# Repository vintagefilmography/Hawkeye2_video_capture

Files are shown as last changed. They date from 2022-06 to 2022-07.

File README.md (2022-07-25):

# SMC02 video capture
This setup consists of a modified projector and the T3i Canon camera. The setup provides the 8mm film capture running at 3FPS and outputs the video in ML (Magic Lantern) RAW format in 1728x972 resolution.  
The purpose of this  readme is to provide the instructions to the user on how to modify the existing 8mm film projector for the video capture directly into the camera using a small off the shelf stepper controller.  
Similar to other projects of this type, this one also requires several modifications to the projector including the light change, and motor change but unlike other projects of this type it provides the DSLR camera capability and RAW video format. The DSLR is used in a slow video mode. 
The stepper controller is programmed to precisely control the stepper motor rotation to provide the proper FPS which matches the FPS of the camera with no flicker. 
System Components  

system-assembly

## Stepper Controller  
At the heart of the system is the SMC02 stepper controller. 
https://www.ebay.com/itm/175028855543

## Stepper Motor  
Use the following stepper.
2.7A for this type motor https://www.amazon.com/gp/product/B00PNEPF5I/
Other steppers may also work but are not covered in this readme.  
If you are planning to pull the projector transport out, then you can use the mounting bracket from this repo.  Check the mechanical parts folder. 

## Pulley
This pulley is recommended. You will also need a sleeve because the pulley bore is slightly larger than the motor shaft. 
Check t mechanical folder for the sleeve sdl.
https://www.amazon.com/gp/product/B07C4QD1BV/

## Belt
This used to be a big problem but with the neophrene Urethane belting that became available it is easy to make your own custom belt.
https://www.amazon.com/gp/product/B07L3W7Z1N  
Follow the following instructions:  
https://www.youtube.com/watch?v=mBtHvPWVgDw

## Assembly
Print out all of the parts from the mechanical folder. If you do not have the printer then you can get them done outside but it will become rather costly. Getting a new 3D printer will probably be cheaper in a long run.
Use a 14"x10"x0.63": piece of wood to mount the components on.  
https://www.homedepot.com/p/Rubbermaid-Black-Laminated-Wood-Shelf-10-in-D-x-36-in-L-4B2500BLA/100200907
Additionally cut two additional pieces of wood size 7"x7"x0.63"and 7"x3.6"x0.63". These will be used as a standoff for the projector transport. 
This will work for the Chinon 2500GL but if other type of projector is used then you will have to figure out how high the the transport has to sit for the proper alignment with the camera.
Assemble the three pieces of wood as shown.
base
Mount the projector transport bracket to the base as shown.
transport_bracket_assembly
Mount the transport onto the bracket using the original transport mounting screws.
The transport mounting will need additional support to prevent the film shake. Use an L bracket  
https://www.homedepot.com/p/Everbilt-3-in-Black-Corner-Brace-4-Pack-13741/300985591
and mount it as shown. Install the spacer underneath the bracket so that the transport sits perfectly vertical. The spacer is included in the mechanical folder. If the transport is not vertical then adjust the spacer accordingly. Tilted transport will cause focus issues.
L-bracket1

Mount the macro lens onto the camera.  
Mount the camera onto the slider.  
Turn the camera on and position it so that the film gate is visible and adjust the zoom so that the film gate covers most of the camera display. Set the slider knobs about half way of the travel. Now, slide the camera on the base board left and right and forward and backwards until the gate is centered in the camera display. Mark the position of the slider  on the base board.  
Remove the camera from the slider.
Place the slider upside down on the table and place a piece of white paper over it. Trace the outline and teh mounting holes as the first graders do.  
https://craft-art.com/tracing-pictures/  
Cut the outline with the scissors and place it on the board so that it is aligned with the marked up outline on the board done in the previous step. Drill the holes. Remove the paper template and mount the slider onto the board using the appropriate size screws.  
Light Mounting.    
The light has to be mounted in front of the gate.    
(This is still work in progress -- will be updated shortly)    
Takeup reel mount.    
Use the microphone stand  
https://www.amazon.com/dp/B07F82BPLV  
Remove the microphone adapter and install the takeup motor bracket.   
Mount the takeup motor onto the bracket using the M3x8 screws  
https://www.amazon.com/gp/product/B076J3W7R4  
Slide the takeup spindle over the motor shaft.  
Slide the takeup reel over the spindle.  
Install an M3 wingnut onto the M3x25 flathead screw and tighten it.  
Slide a flat M3 washer over the screw shaft to create the "clutch" mechanism.  
Push the screw through the spindle center until it engages with the motor shaft.  
Turn the wingnut in until snug. The tightness will determine the amount of pull on the film.  
You do not want it too tight becaue it can cause film damage.  
Solder two wires to the motor terminals.  
Connect the wires to the speed controller.  
https://www.amazon.com/gp/product/B071H2YQG5/  
Connect the controller to the 12VDC source.  

Proceed similarly with the supply reel. 
Remove the mic adapter from the microphone stand. install the reel mount assembly onto the mic stand.
Install the small clip onto the reel spindle using a small metal pin. 
https://www.amazon.com/Neiko-50412A-Assortment-Storage-Pieces/dp/B076B4WT1V/

supply-reel-mount_assy
Controller installation  
Afix the mounting bracket onto the base board by using two wood screws.
Mount the SMC02 cntroller onto the controller mount but sliding it into the mount opening all the way until locked in. 
Wire up the controller as shown.
smc02-wiring

Stepper Installation  
Mount the stepper onto the stepper racket using the M4 screws and nuts.
Mount the sleeve over the motor shaft and then side the pulley over the sleeve. Do not tighten the locking slugs. 
Align the pulley with the transport cam and install the belt. Slide the stepper assembly left and right on the base board until the belt is aligned and has 
good enough tension on it. Mark up the stepper bracket location.  
Remove the stepper from the bracket and install the bracket by using 2 wood screws. Mount the stepper back onto the bracket and install the belt.

## Tuning the Stepper  
The FPS (fremes per second) of the film transport is not the same as the stepper RPS (revolutions per second) due to different pulley diameters.  
The ratio has to be determined experimantally.  
Connect the controller to a 24VDC source and turn the power on.  
The display should show initial operaional settings.  
initial-display  
Press and hold the control knob until the unit goes into the setup mode.  
setup1  
turn the knob clockwise until F03 is displayed.  
The bottom line will show the default 010.0  
Pres the control knob again to enter the bottom line edit mode.  
The decimal value will be flashing.  
The decimal value can be changed by rotating the control knob, but leave it at zero.  
Press the knob again and the least significant digit will be flashing. Change it to 9.  
Press again and change the next digit to 2.  
Press again and change the first digit to 3.  
The lower display should  be reading 329.0 with number 3 flashing.  
Do the extended press to get out of the setup mode.  
Now 329.0 should be displayed on the top line and 0000 on the bottom line.  
That sets the stepper RMP.  
Now we have to set the running mode for continuous operation.  
Do the extended press again to get into the setup mode.  
F01 will be displayed on the top line and P01 on the bottom line.  
Press the control knob and the bottom line should be flashing.  
Change the bottom to P03 by rotating the control knob.  
Do the extended press to get out of setup.  

Quick Test  
Press the CW button - the motor should run clockwise and the film cam should rotate at 3 RPM.
Press the stop button. The motor should stop.  
Note: If the motor rotation is reversed then reverse the green and black wire connections.
Another Note: The reverse speed is set to 10 rpm which is slow. If planning to use the reverse operation then the reverse speed is set by changing the F05 field  
by using similar procedure as listed above.  

## Camera  
The camera used should be capable of caustom frame rates. 
Sony A7iii supports custom rates but it is quite expensive.
An alternative is to obtain the T3i body and add the macro lens. 
The stock camera does not support the custom frame rates but there is a custom software available that enables   
custom frame rates and raw video.
Listed below are the instrustions on how to install Magic Lantern and set it up for FPS override, but before that here is a quick overview:  
Download the build to your PC and unzip it.
Format the SD card by the camera itself.
Make sure your battery is fully charged. That is very important. You can ruin the camera if you do not follow these instructions carefully. 
Install the SD card into the camera and power it up.  
BTW - going forward any time you open the SD card cover, do not remove the  SD card immediately, wait for the red led to stop flashing.
Set the camera to Manual mode
Press the MENU button 
Go to the second last screen and press the Firmware button.
Double check the Magic Lantern instructions  
https://builds.magiclantern.fm/600D-102.html  
Do the update  
Recycle power and you are ready to go.  

Refer to https://magiclantern.fm/  
for more details.  
Specifically refer to this page for the T3i:  
https://builds.magiclantern.fm/600D-102.html  
For setting up the camera refer to:  
https://www.youtube.com/watch?v=NYGseJ7Sofk  
https://www.youtube.com/watch?v=RvZHmOgzm2Q&t=6s  
Thsese two videos give you a pretty good idea on how to set the 3 FPS but there are some devil details missing.  
Will try to cover those in here.  
Set the camera to Movie mode.  
Turn the camera on and turn on live preview.  
This will start the Magic Lantern software.  
Then press the delete button.  
The settings screen will pop up.  
Go to  the Movie screen:  
movie-setup  
Select FPS OVerride. Press enter to turn it on.  
fps-override-on  

Then press the Q button on the T3i. Other camera types will have a similar button.  
The FPS Override screen will pop up.  
fps-override-2point5  
Hit the Q button.  
fps-set  

Position highlight over desire FPS and hit Enter. Set desired FPS to 3 by using the left and right keys.
  
 fps-set-to-3  
Press enter again to go bach to the FPS Override screen. Select the "Optimize for" entry and hit Enter.

optimize  

Select High FPS  

high-fps  

After selecting High FPS the camera will go back to the FPS override screen.  

fps-override-1  

Select Advanced Mode.  

advanced-mode  

Select Timer B. Leave it as is for now but remebmer how you got to this point becase you will need it later   
for sync procedure.

tune-fps  

Go back to the FPS Override screen.  

fps-override-2  

The shutter speed can be changed on the Expo screen.  

shutter  

The shutter rspeed can also be changed while scanning the film by using the main dial. Check the manual fo main dial location (tp of the cam).
The light should be bright enough so that the shutter speed is 1/300 or faster. If the shutter is too slow than some image degradation can happen.
It is to be noted that even at this fast shutter setting, due to low FPS you could experience some jello effect. The jello effect exhibits itself as a 
the video shrinking and expanding as jello and can be very annoying. The cause is the rolling shutter which stores one image line at a time. At slow scan   
there is a shift in the top of the image as compared to the bottom of the image i.e. by the time the scan gets to the bottom the scene has changed somewhat.   
But on a positive note, the postprocessing done in DaVinci Resolve almost completely eliminates this degradation.   

## Macro Lens
There are many out there that will do the job.  
Venus Laowa is a pretty good pick. It has more than enough magnification and good image quality and it is reasonably priced.
https://www.venuslens.net/product/laowa-25mm-f-2-8-2-5-5x-ultra-macro-2/  

## Sync procedure
Back it off and turn it away from the gate and point it to the cam (pulley). Adjust the speed control on the controller until the cam appears stationary. Actually it will jump up and down and possibly drift slowly. If the drift cannot be stopped by the speed control, then adjust the Magic Lantern Timer B to minimize the drift. Once done, refocus the camera back onto the gate. With this procedure I can run for several thousand frames without sync issues. It should be noted that the transport should be in good condition ensuring constant speed. It still may be possible that the drift catches up with you depending on the initial condition. In that case just run one step up for a few minutes if the drift is from the top, or one step down if the drift if coming from the bottom. Then switch back to the original speed. After that you can run for several thousand frames without sync issues


## Operation

Load the film.  
Plug in the 24V and 12V external power sources. 12V is for the takeup and 24 is for the controller.     
Make sure that they are not reversed which can result in the takeup motor damage. 
Turn the light on.  
Connect the camera HDMI port to a monitor.  
Turn the camera on and press the live view button. This will start Magic Lantern. 
Press Live View again to start recording.  
Press  the CW button on the controller.
Once done with the recording, stop the camera by pressing the live view again abd stop the controller by pressing the stop button.  
Remove the SD card and copy the MLV (Magic Lantern Video) to a PC.  

## Post Processing  
Download the MLV app from:  
https://mlv.app/  
Install the app.  
Open it up.  
Drag the video into the session window as shown:  
mlv-drop-video  
Expand the transformation entry on the right hand side and turn the Upside down control on.  

upside-down  
Review the video to see if any sections have to be retaken. This app has pretty limited video edit capabilities  
but it has lots of export formats suitable for popular video editors.  
Open up export settings from File pulldown:  
  
Select DNG uncompressed format if exporting to Resolve.  
The DBG images take up lots of space but in return contain the raw information that can be utilied in DaVinci Resolve.  

Export the video by using File->SaveVideo into the directory of your choice.  
Close the mlvApp.  

## DaVinci Resolve  
Open up Davinci Resolve and drag the DNG images into it.
  
  
Right click on the clip and create the new timeline:  
  
Click on Custom Settings and change the frame rate to what you need.
Switch to Edit Mode:  
  
In the transform area on the right hand side, rotate the video by 180 degrees.  
  
Switch to color edit mode. Select Camera Raw and Decode using Clip as shown:  
  
Adjust exposure as shown:  
  
If the video shows a jello effect then this would have need adjustment.  
Go back to the edit mode:  
In the transform area on the right hand side scroll down to Stabilization.  
Set mode to Perspective.  
Turn on zoom and then adjust stabilization parameters as needed. It will be a trial and error process. Too little and the  
video will be wavey and too much will cause severe clipping and loss of resolution.  
  
Click on the stabilize button to run stabilization. It may take a while. 

https://www.youtube.com/watch?v=u6UWJCQB7n0  
If the video has noticable jello effect then apply the Resolve stabilizer as shown the video below.  
https://www.youtube.com/watch?v=73zwjGcbhP4  

### Slow Motion interpolation with speed change  
Save the VirtualDub2 video as a sequence of tiff images first.  
Select all images and drag them into the media window of DR (DaVinci Resolve).  

You will get the images shown as a clip in the media window.  
  
 
Right click on the clip, select the click attributes and set the frame rate if necessary  
but you can leave it as is since the frame rate change can be done later.  
Right click on the clip and create the timeline from it.  
  
   
Switch to Edit Mode.  
  
   
Click on project settings  
  

Scroll the settings all the way down and change the retime process to optical flow (more info available here  
htps://www.youtube.com/watch?v=m5cO3ZTfSr4 ).  
  
  
Save the settings.  
Now, right click on the clip and change the speed to whatever FPS needed.  
  
 
Change the FPS to whatever required.   
  
 
Make sure that Ripple sequence is checked off. If not the clip duration will not change and the clip will be truncated.   
Click on the change button. Note the clip duration change in the timeline window.  
  
   
Once done, complete other changes as necessary and then export the video by switching to deliver mode.  
  
   
Change the video format to whatever you like.  
  

Add to render queue  
  
 
And then start render.  
  

### Interpolation without Speed Change  
The above instructions were for interpolated frames that result in smooth slow motion speed.  
In many cases however we want to interpolate the frames but want to maintain the original speed.  
In order to do that just follow the above instructions but do the following changes.  
1.	Make sure your project settings are set to optical flow for retiming.  
2.	Before creating the timeline set the clip attributes FPS to 60 FPS.  
3.	Create new timeline  
4.	Using the above procedure change timeline speed to 24 FPS or whatever final speed you need  
The rest is the same as the above procedure.   
Here are the details.  
Project settings optical flow selection.  
    
    

Drag the images into the media window. Make sure all images are selected.  
  
   
Switch to edit mode if not already there.    
  
   
 Right click on the images file in the media window and select clip attributes.  
 Set clip FPS to 60 or whatever interpolation rate you prefer.  
   
Click on OK.   
Right click on the clip again and create the timeline. The timeline create window pops up.  
Click on custom settings.  
  
 
It is to be noted that in version 17.2 of DaVinci the timeline popup window is a bit different.  
It does not have custom settings but it has a button to use the Poject Settings.  
Make sure that button is not checked off. 
  

Select Format tab and set the desired interpolation FPS.  
  
 
The new timeline will show up in the timeline window.  
Right click on the timeline in the timeline window and select Change clip speed.  
  

Change clip speed back to normal speed i.e. 24 or 18 FPS or whatever the original speed was.   
You can also go lower if slow motion is preferred. Make sure Ripple sequence is checked off.  
  
 
Note the clip stretching out after the speed change.   
If t does not then make sure that Ripple sequence is checked off.  
At that is basically it.   
You can test run the clip to make sure that additional frames got added by stepping through the video (left, right arrows).  
The next step is to render and save the video.  
Switch to Deliver Mode.  
  
   
Select proper video format and add to render queue. 
  
   
Start rendering.  
  
 
And that completes the procedure.

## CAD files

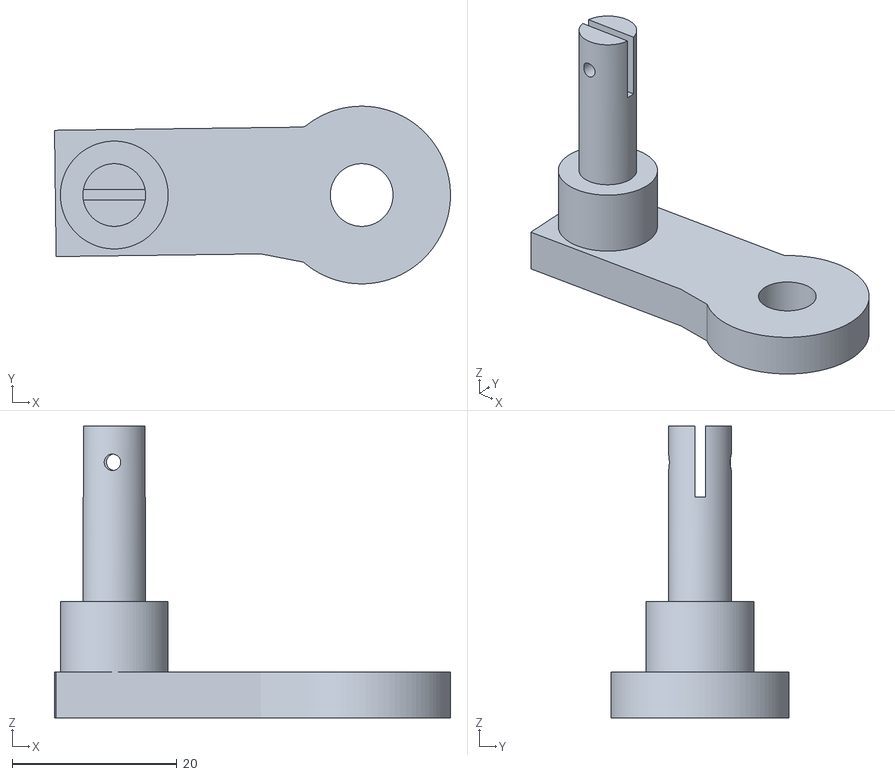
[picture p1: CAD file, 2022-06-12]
mechanical/reel-mount_assy.stl
48.1 x 21.6 x 35.4

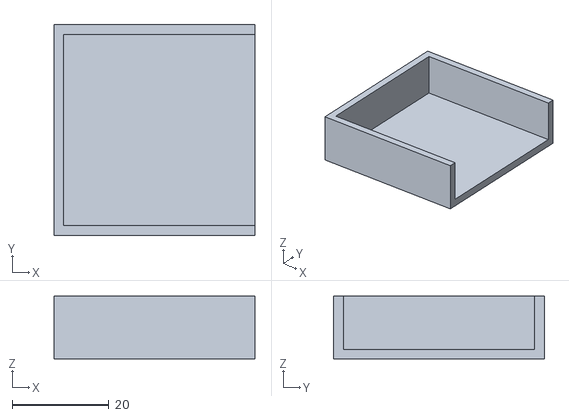
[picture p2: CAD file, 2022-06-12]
mechanical/diffuser.stl
41.5 x 43.5 x 13.0

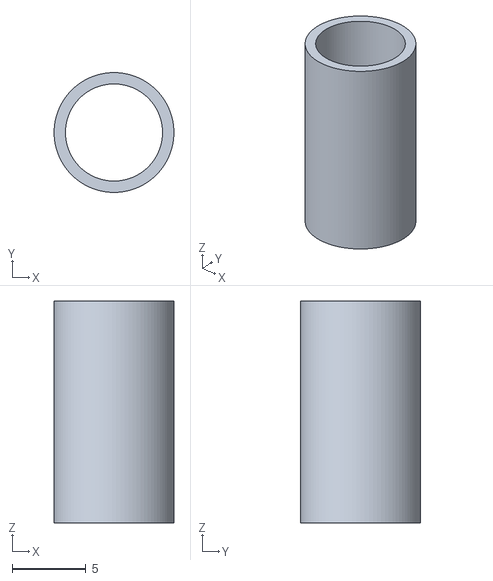
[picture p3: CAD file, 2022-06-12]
mechanical/sleeve.stl
8.10 x 8.10 x 15.0

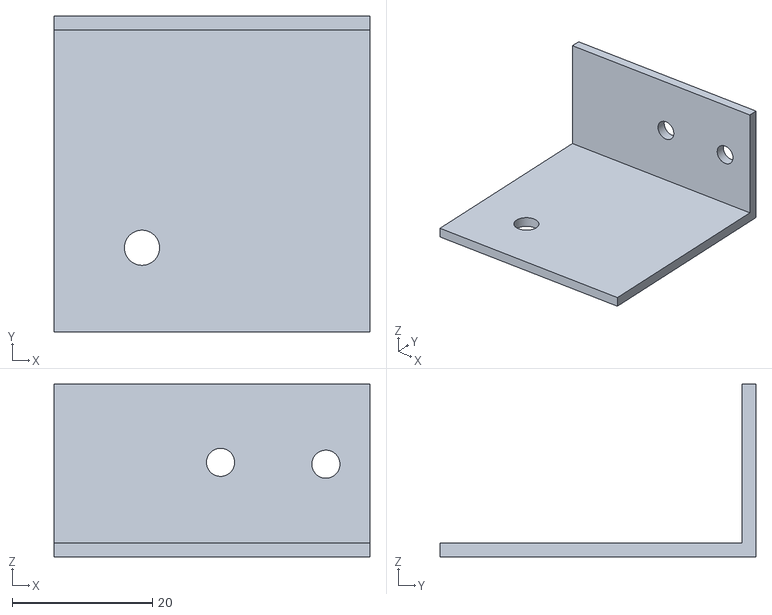
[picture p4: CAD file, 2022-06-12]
mechanical/roller_mount.stl
45.0 x 45.0 x 24.6

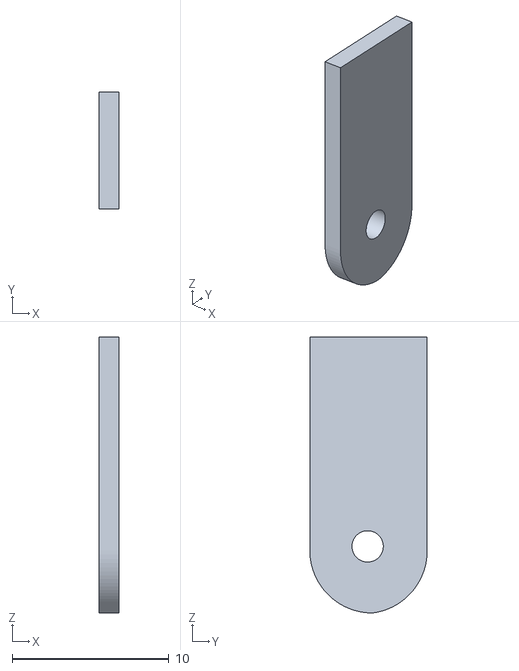
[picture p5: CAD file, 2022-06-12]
mechanical/clip.stl
1.27 x 7.50 x 17.6

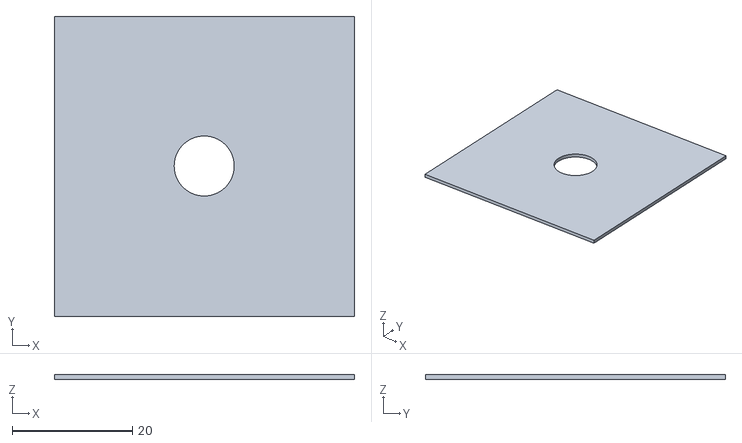
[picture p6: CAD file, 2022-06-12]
mechanical/cam_spacer.stl
50.0 x 50.0 x 0.8

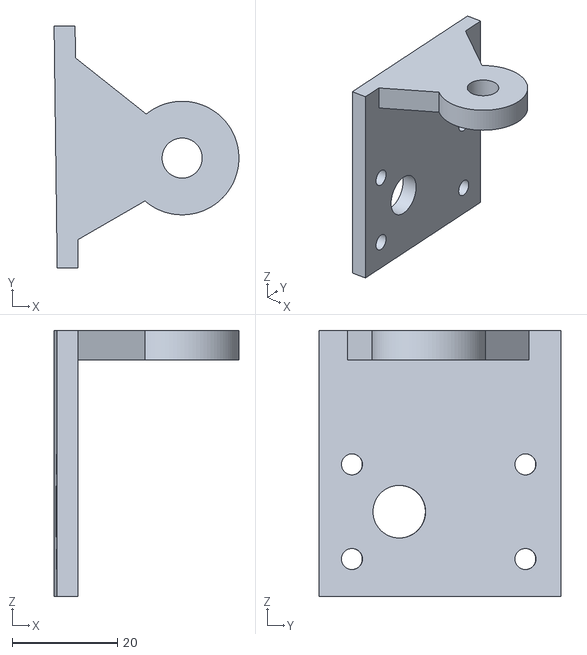
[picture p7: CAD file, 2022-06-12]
mechanical/takeup_mount.stl
35.2 x 46.0 x 50.6

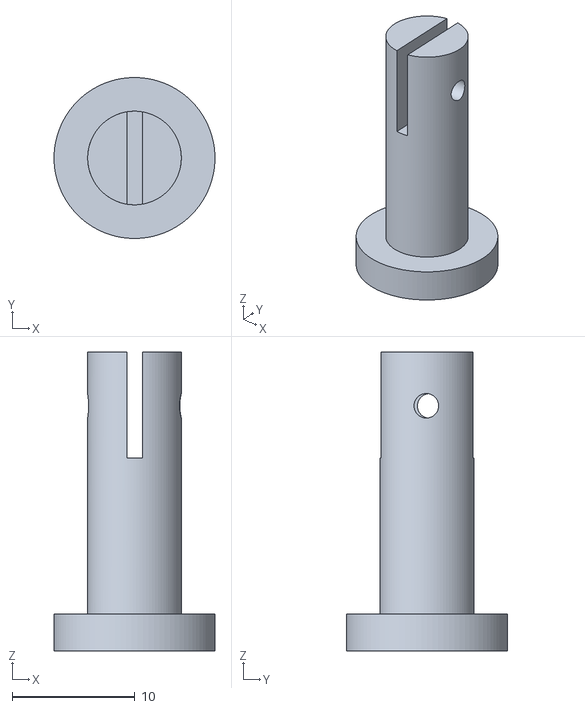
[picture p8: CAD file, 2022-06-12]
mechanical/reel-mount.stl
13.1 x 13.1 x 24.3

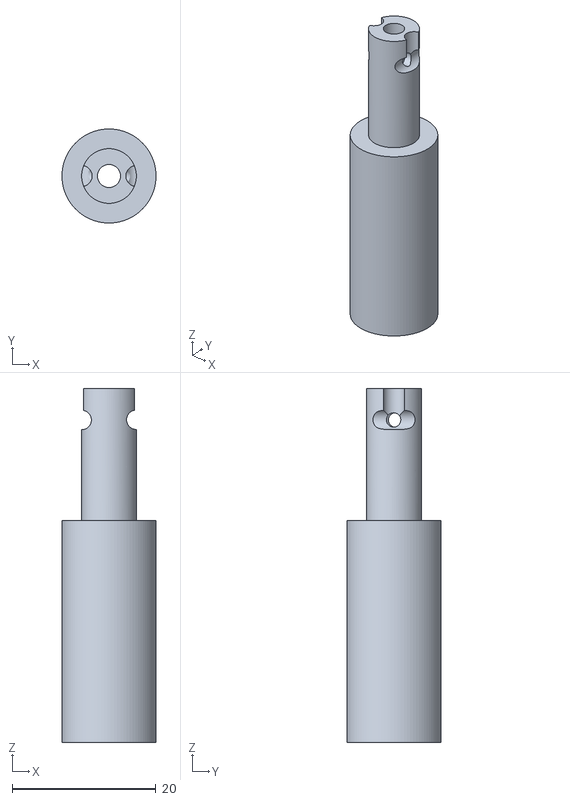
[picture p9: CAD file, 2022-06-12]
mechanical/takeup-spindle.stl
13.1 x 13.1 x 49.3

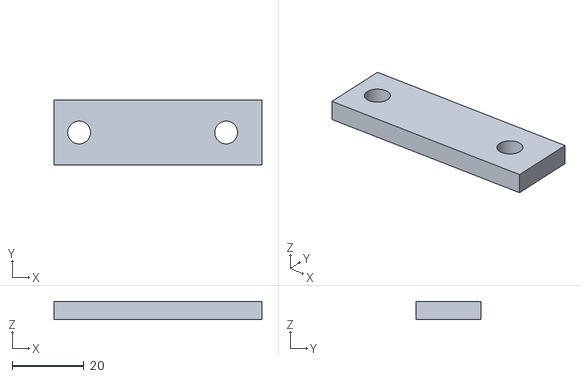
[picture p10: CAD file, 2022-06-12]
mechanical/spacer_alignment.stl
58.0 x 18.0 x 5.10

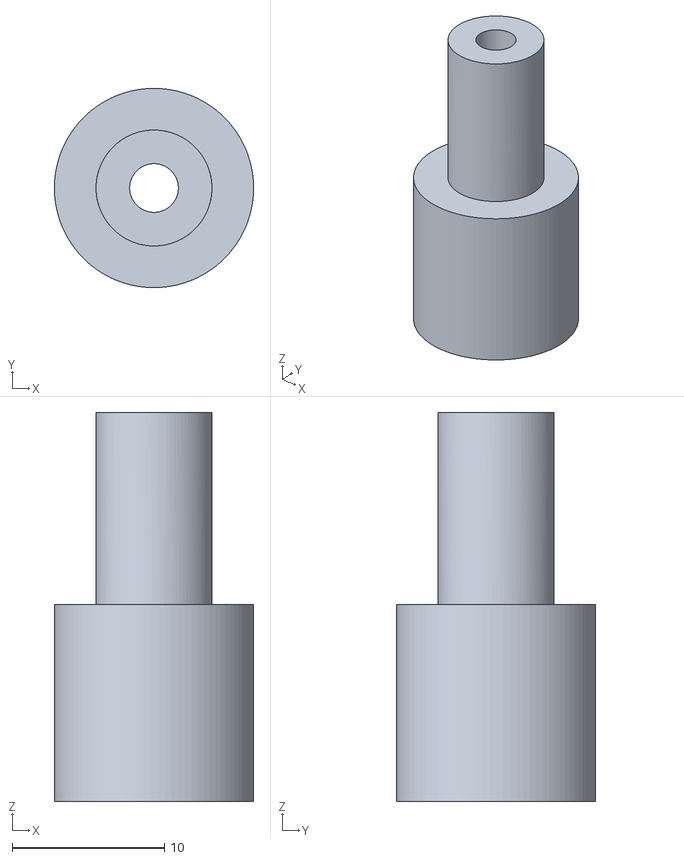
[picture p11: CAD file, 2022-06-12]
mechanical/takeup-spindle1.stl
13.1 x 13.1 x 25.6

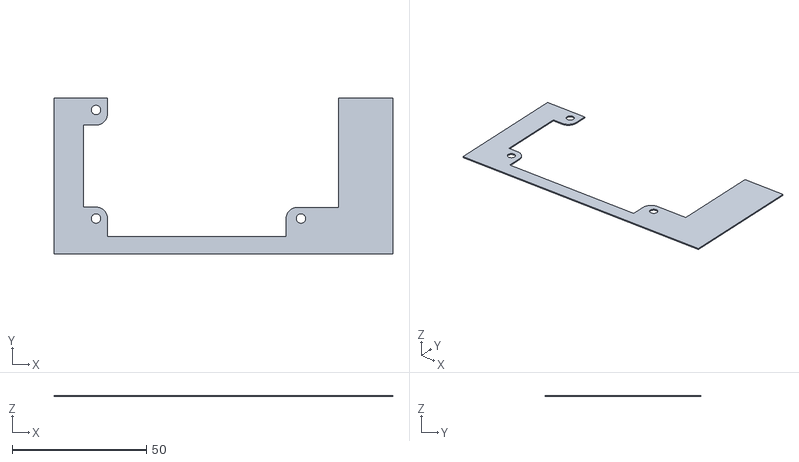
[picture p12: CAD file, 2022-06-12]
mechanical/chinon_bracket-test.stl
126.1 x 58.0 x 0.5

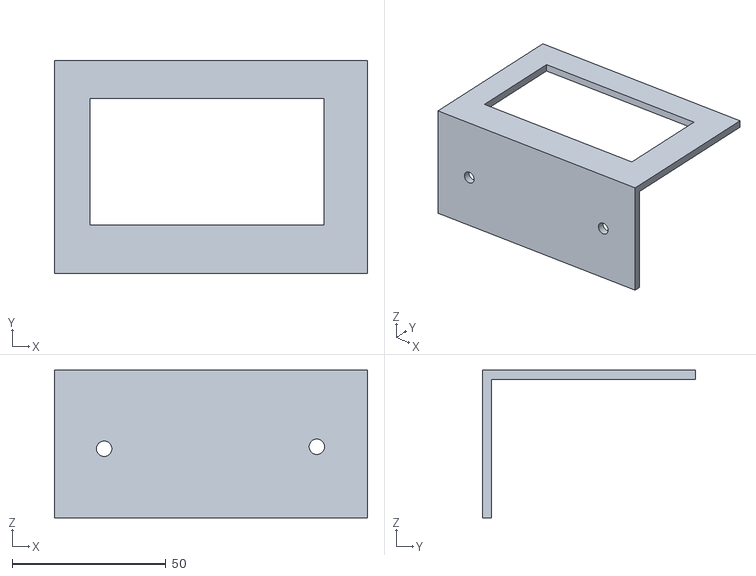
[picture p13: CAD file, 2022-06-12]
mechanical/controller-mnt.stl
101.7 x 69.2 x 48.0

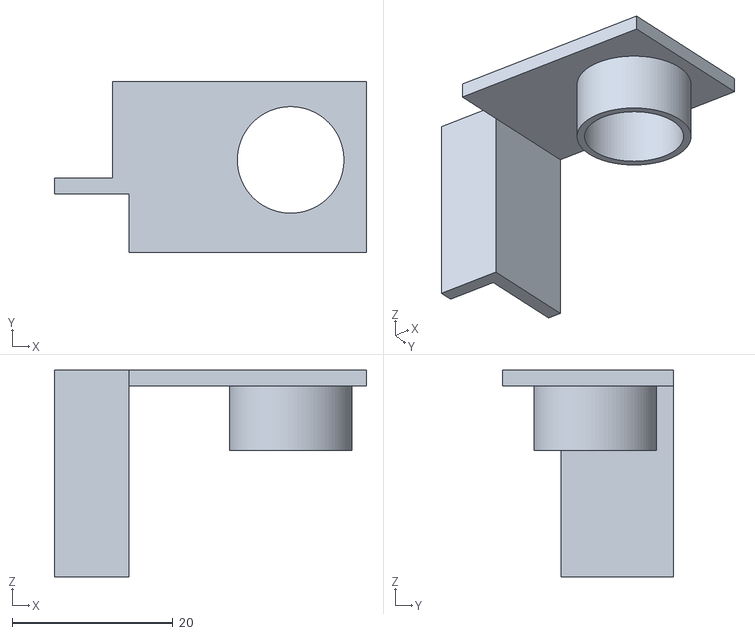
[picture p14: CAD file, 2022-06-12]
mechanical/light_mount.stl
38.8 x 21.3 x 25.7

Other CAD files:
mechanical/chinon_bracket.stl
mechanical/Pulley_Support.stl
mechanical/takeup-template.stl
